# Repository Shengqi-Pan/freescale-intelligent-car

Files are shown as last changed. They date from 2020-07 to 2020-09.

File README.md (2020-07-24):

飞思卡尔全国大学生智能车竞赛 直立节能组

# 项目日志

## 6.24

1. 测定陀螺仪和加速度计bias和比例

2. 调通了卡尔曼滤波

3. 测定小车过轴线时的倾斜角，设定其为平衡角，23.8°

4. pd参数调节，最终角度确定为23.87°，角度环参数P=2000 D=50

## 6.25, 6.26

1. 调了下电磁，实现基础的转向

2. 控速有点迷，一直没找到bug，进展不大

## 6.27

1. 找到控速bug, 因为限幅使得控速的角度附加全部处于死区，调节不过来

其他可能导致bug的原因：

- P太大

- 角度梯度太小

- angle_bias太小

- 限幅值太小

- 设定速度太大

## 6.28

1. 找到了疯狂振动(拖拉机)的原因, 角度环的D太大, 从59改到13后没有问题

## 6.29

1. 调通了左圆环，步骤如下:

    - 判断是左圆环or右圆环

    - 判断前瞻到切点

    - 判断车轮到切点，并将控制权移交竖电感

    - 用陀螺仪判断转向转过90度，此时将控制权移交横电感

    - 自然出环，待添加出环时屏蔽圆环状态的代码

2. 右环电感归一系数待调

    - 可考虑加偏置而不是单纯归一化

    - 考虑将1中的第二第三两个判断条件直接去掉（或许加上这两个条件实际意义不大）

## 7.5

1. 完成了速度的部分提升

    - 重新分割转向pd，加大d的作用

    - 加入抱死安全措施

## 7.6

1. 在高速下进圆环初步实现，问题比较大

2. 控速换成了PI控速，控速较稳

3. 小弯转向飘逸待改进？

## 7.7

1. 初步实现圆环进入，具体方法为通过补偿在圆环切点电感值减小的特点，产生交汇移交控制权给竖电感完成进环

2. 加入出环屏蔽，但圆环出环形成循环，出环时漂移，需要解决

3. 圆环入环准确率还不高，考虑角度补偿

4. 通过减小圆环中的偏差值圆滑圆环的过弯，圆环中莫名其妙抱死？

5. 可调节的有判断圆环的条件，入环的延迟距离，竖电感的归一化值，竖电感转向的pd

## 7.8

1. 完成入环2.0版本，出环1.0版本

    - 入环通过差值先减小后增大的现象设定阈值，完成入环的判断。

    - 出环通过减小出环时的deviation，同时增大d以补偿减小的deviation。

## 7.9 

1. 中断时间从1.25ms改为1.5ms

## 7.10

1. 通过限制angle_bias完成了过坡

2. 判坡用了个临时条件，最终决定加中间电感

## 7.14

1. 加入加速度计限幅，上下坡明显改善，直立环很硬

## 7.15

1. 杆子降低，速度回归，重调了转向和直立环

2. 去掉了转向陀螺仪补偿，入弯减速去掉但会掉速

3. 需要解决转弯减速的问题

## 7.16-7.23

一直在调结构改板子

## 7.24

1. 换新的电机调了一套比较好的pd，有时候转弯完全眼瞎，待调

> 看一下目前的代码和以往代码的区别，可能还存在一些能提高车辆稳定性的异常处理思路:
17代码：
    1. 编码器的加速度对加速度计的修正
    2. 陀螺仪零飘测定，或许会有效果吧？不加问题也不大
    3. 入弯低头补偿掉速，出弯抬头减速
    4. 速度超出允许最大速度一定值（200，400等），强制抬头

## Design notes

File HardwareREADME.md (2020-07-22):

# **硬件设计与调试**

## PCB Version 3.0

电磁检测插在MCU母板上

不带5V和12V稳压的电机驱动

底盘换成PCB，把无线充电方案、5V、12V稳压和MCU母板放上去

-----------------------------;

无线充电方案

## **TODO LIST**

### **母板V2.0和电磁检测V2.0板子硬件调试**

- ~~更换左侧竖电感~~

- ~~调节四个电位器，使左右横竖电感的AD采样值对称~~

- ~~直立控制测试~~

- ~~无线串口接收测试~~

---------------------

**7.14~7.16：基本正常**

---------------------

**已更换新版，该版母板和电磁寿终正寝。**

### 车底盘，PCB上把5V、12V稳压、母板放在一起

- ~~5V和12V输出的单点接地 SGND、PGND~~

- ~~按键S2~S5、RST封装修改~~

- ~~供电开关按键修改，要能流通大电流~~

- ~~可能需要修改电机控制、编码器、陀螺仪、无线串口的接口位置~~

- ~~需要增大一些接口之间的间距，以避免排线插接冲突~~

- ~~TPS630701封装修改，便于焊接和虚焊检查~~

- ~~检查供电接入开关、母板5V开关、驱动板12V开关是否加进去了~~

- ~~TPS61088封装修改~~

- ~~PCB尺寸定义与检查~~

- ~~给ICM留出2.5*1.5的空间~~

-------------------------------;

**7.15：车底盘，母板v4.0已制板**

-------------------------------;

**7.19：TPS61088升压12V无输出，计划7.20重焊，再测试一下thermal pad焊盘和PGND的连通性**

- 理一下国赛电路合集里面的61088升压

- 修改大电流回路的一些器件封装，包括电感换成功率电感。

- 板子上加入日期

**7.19：烧了两块TPS61088（有一段时间能够正常输出过），目前还没有查出问题出在哪里，拿TPS630701的输出接了EN脚，又把630701烧了......**

-------------------------------;

**7.20：准备更换12V稳压芯片方案**

- 除复位键按钮，剩余按钮改为拨码开关

- 稳压的5v可以考虑直接供给单片机，尽量不出现一个端子接两线的情况

- 主板的电感为六路电感，主板ad读取接口可以加上P06, P12, P16，上面三个引脚没有其它用处的话作为六路电感多出的两个电感

- 若单片机需要控制充电，任意空闲的GPIO留出作为控制引脚

- 也可多留两个废物引脚当备胎

- 可以考虑加蜂鸣器，P37，参考逐飞

### 电磁检测PCB

- 多加一个OPA2350，增加一路电感AD采样用于判坡

- 在母板上留出的尺寸空间也要作修改

- ~~**！！！要修改滤波的方式，更改输出滤波电路，RC串联加稳压和反向限幅**~~

- ~~**直接修改OPA2350为OPA4377，增加一路电感，暂时空出一路**~~

- ~~**加一路OPA2350，仿照OPAMOD模块**~~

----------------------------;

**7.13：电磁检测v2.0已改完制板，贴片电阻改为0603封装，电容为C0805**

**7.17：焊完了电磁检测的板子，毛刺问题、电磁测量值的非线性问题。**

----------------------------;

### 电机驱动板

----------------------------;

**7.16：焊接和调试，发现一个小问题：由于自举电容的机制约束，HIP4082驱动全桥的上管在原理上应该不能到100%占空比，这一点需要在之后的软件里面测试和注意。**

**7.20：在考虑是否把电机和驱动分两块芯片供电，34063升压可能电流负载能力不足。**

### 无线充电方案

- 恒功率充电 or 简单的全桥整流？

---------------------------;

**7.17：目前的想法是，接收端640KHZ LC谐振，然后四个肖特基二极管全桥整流，再稳压到12V，再接入SuperCap组，在线路上做电压电流的采样，送入单片机做乘积得到实时功率，然后PID控制MOS通断（BUCK）来控制平均充电电流（或者电压），做到稳定充电功率的效果**

**References：**

> [飞思卡尔恒功率无线充电（上）](https://cloud.tencent.com/developer/article/1651860) \
> [飞思卡尔恒功率无线充电（中）](https://cloud.tencent.com/developer/article/1651861) \
> [飞思卡尔恒功率无线充电（下）](https://cloud.tencent.com/developer/article/1651862)

**7.19：芯片选型**

- 备选器件

  - 前期12V转5V稳压：TPS5410，REG104，TPS561201

  - 全波整流转12V：TPS54360（需要额外注意设定其开关频率）

  - 电容：NPO高频电容

  - 电感：功率电感

**7.20凌晨：电路原理图基本完成，下一步更新封装和画PCB**

### 元器件

- OPA2350

- 100K电位器

- 稳压管

- 47K电阻

- TPS630701

- 61088外围电路元件RLC

- 工字电感

--------------------------;

**7.16：买了新一批器件**

**7.19：准备更换外围无源元件选型**

- 贴片陶瓷电容

- NPO高频电容

- 闭环控制、电压检测、反馈回路的电阻均要换成高精度低温漂电阻

**7.20凌晨：准备买元件**

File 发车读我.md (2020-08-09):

# 拨码开关

|拨码作用|左侧|右侧|
|---|---|---|
|出库方向|向左出入库|向右出入库|
|速度1|正常速度|快速|
|速度2|慢速|最慢|
|圆环开关|开|关|
|充电电量|少|多|
|充电电量|开|关|

# 摄像头

屁股坐地上摄像头面向正前方，不直掰一掰

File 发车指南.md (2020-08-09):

# 裁判手册中的说明

比赛流程控制：

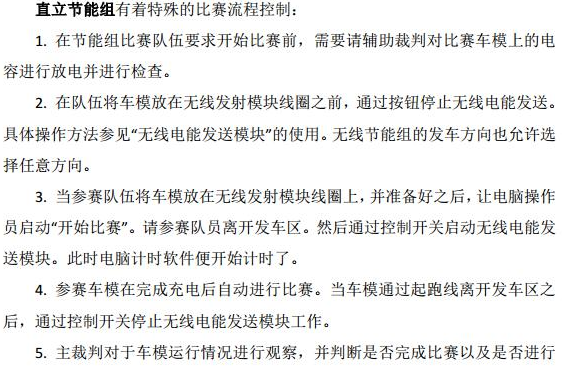
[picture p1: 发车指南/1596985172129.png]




充电线圈的标志可能如下，十字代表中心：

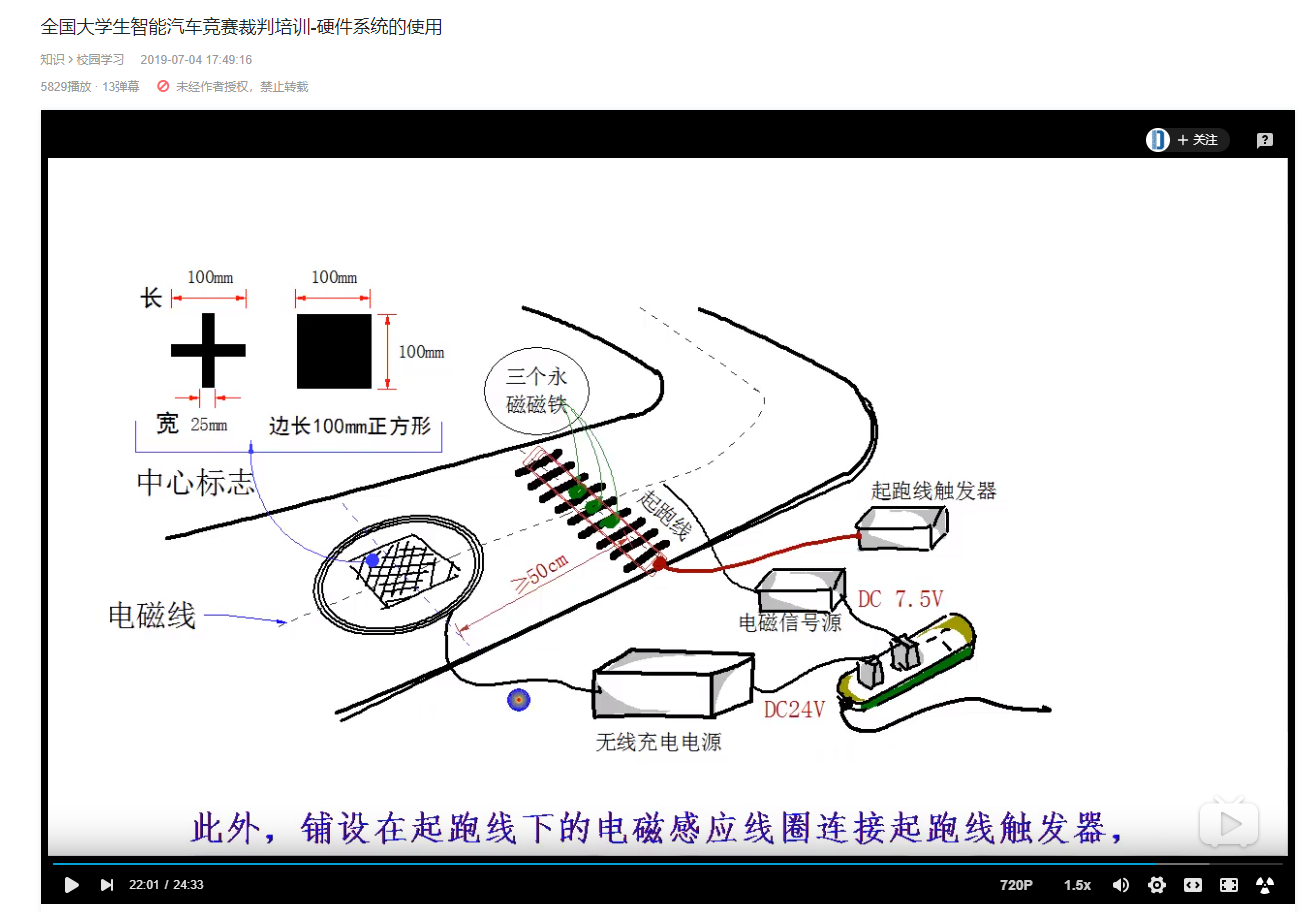
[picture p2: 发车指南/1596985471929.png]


# 试车阶段需要做的事情

1. 找一个好的出库方向试跑一圈

2. **接上无线串口并在电脑上打开示波器点击run和绿色的运行，打开isp烧录软件**
3. 大概1min时间摸一摸最优的充电位置，注意放电到0再充电
4. 目测圆环大小，烧录圆环测试代码并推行测试，

# 发车检查

**拔掉无线串口！！！！！！**

1. 擦轮并检查两轮轴固定，如下图：

   - 轮胎前后转动齿轮跟随良好
   - 轮胎左右位置固定，即轮胎不会往外拉出来

   

2. 检查摄像头

   - 是否打开，是否90度（如果当前角度入库过晚，考虑把固定的胶撕下来（不要脱落），ccd变为90度）

3. 检查电机驱动是否打开（摁下），电源总开关是否打开（向下），五伏开关是否打开（向右）

4. T头是否全部插紧

5. 外部飞出的导线是否会磨到齿轮

6. 拨码开关拨到适当的位置，第一圈跑应当除了第一个拨码开关控制左右出库（视情况而定）外，全部打向左侧

7. 检查其他接线是否牢固，此项基本问题不大，注意编码器即可

8. 将车辆摆放到正确的位置

# 应急处理

**若车辆冲出赛道，不计成绩的情况，立刻重新发车**

1. 第一圈跑完可能出现的情况及应对方式：

   - 出库偏晚或偏早

     换代码，视频沟通，直接**烧代码**即可

   - 进圆环跑飞，跑出赛道外

     立刻停车并**关闭圆环拨码**4，尝试完成比赛，与此同时btk根据现象修改圆环代码，烧录并发车

   - 入库偏早或偏晚

     偏早不太可能吧...

     偏晚的话调节摄像头到平行位置应该就可，如果上坡摄像头磕到改变角度可以考虑用螺丝刀和十字架**把摄像头上下旋转的控制螺丝螺母拧紧**

   - 电量不够跑完一圈赛道

     视距离终点的距离而定能量拨码 ：距离不远->6拨码向右打，距离较远->5,6全部向右打，实在不行则烧代码。

   - 顺利跑完，8说了，i了i了

     用万用表检查一下跑完时还剩多少电压

     - 如果还剩电压比较多，如4v，将能量拨码5向右打，冲一圈。
     - 如果剩余电量不是很多，提速，将速度拨码2向右打，冲一圈

2. 其他情况应急处理

   - 电磁杆撞断：尝试用黑胶布补上，实在不行就用旧杆
   - 竖电感撞掉：尝试用黑胶布补上，不行就缠在杆子上，关闭圆环
   - 无法判库：尝试用距离进库

# 约定

如果改动要烧的代码涉及到拨码档：

- 比如需要的速度比拨码的最高档还要高，则改动的代码直接提高最高档位速度
- 如需要的速度比拨码最低档还要低，则改动的代码直接降低最低档位速度

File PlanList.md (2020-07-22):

# **PLAN LIST**

## **7.21**

- 软件：新底盘调控速2000，直道、弯道、上下坡

- 硬件：改底盘

  - 电感改成功率电感封装

  - 630701外围电路换成63070，加两个电阻

  - 5V稳压加个防倒灌环节（参考别的技术报告）

  - 61088的GND、VIN、VOUT铺铜走线调整

  - 再留出两路AD给电流采样电阻的正负电压

- 硬件：买元器件

  - 功率电感1.5uH

  - TPS63070

  - TPS561201

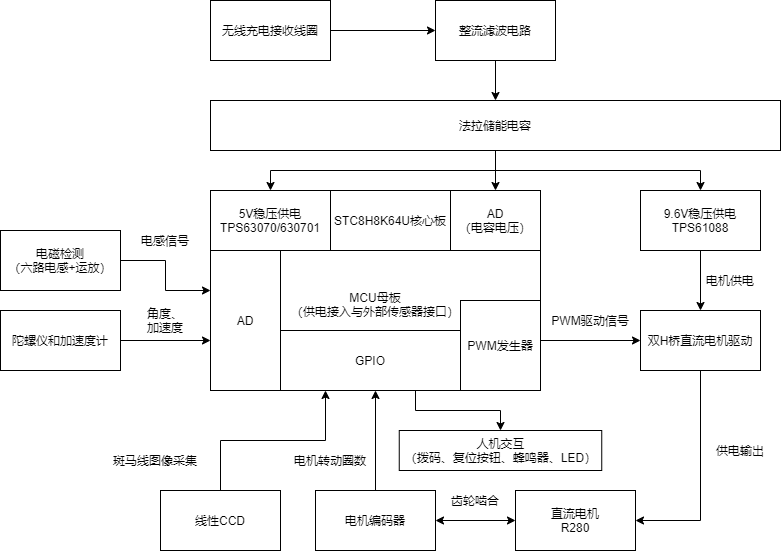
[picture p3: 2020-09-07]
硬件模块总览.png

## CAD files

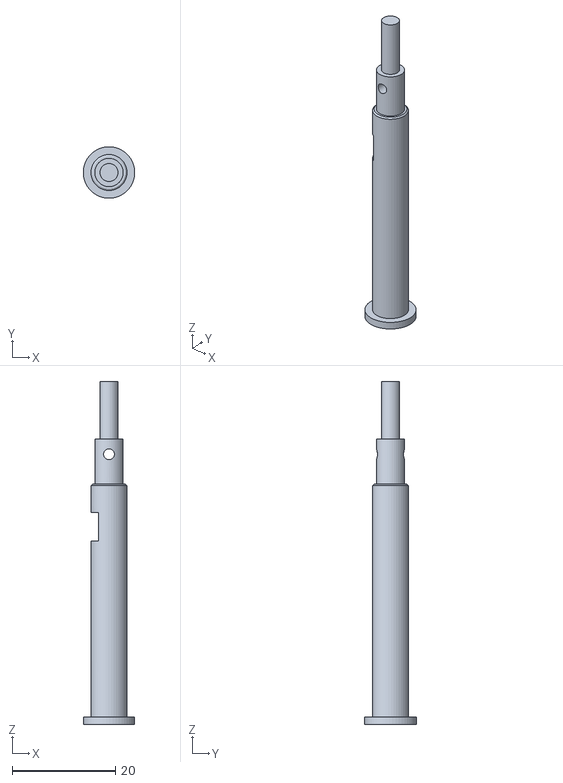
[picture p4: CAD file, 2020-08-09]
轮胎轴3D打印模型/3.stl
9.98 x 10.00 x 66.6

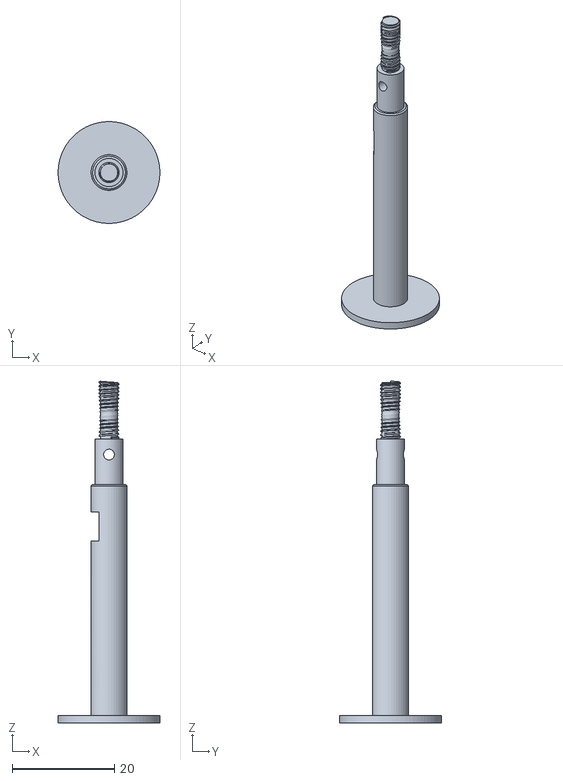
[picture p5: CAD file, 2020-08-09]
轮胎轴3D打印模型/2.stl
19.9 x 19.9 x 66.9

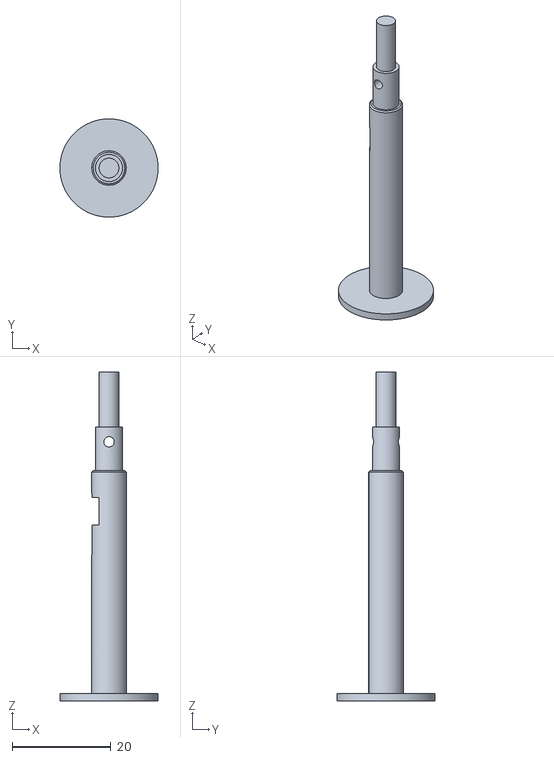
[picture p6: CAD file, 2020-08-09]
轮胎轴3D打印模型/1.stl
19.9 x 19.9 x 66.6

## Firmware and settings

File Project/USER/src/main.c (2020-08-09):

/*********************************************************************************************************************
 * COPYRIGHT NOTICE
 * Copyright (c) 2020,逐飞科技
 * All rights reserved.
 * 技术讨论QQ群：一群：179029047(已满)  二群：244861897(已满)  三群：824575535
 *
 * 以下所有内容版权均属逐飞科技所有，未经允许不得用于商业用途，
 * 欢迎各位使用并传播本程序，修改内容时必须保留逐飞科技的版权声明。
 *
 * @file            main
 * @company         成都逐飞科技有限公司
 * @author          逐飞科技(QQ790875685)
 * @version         查看doc内version文件 版本说明
 * @Software        MDK FOR C51 V9.60
 * @Target core     STC8H8K64S4
 * @Taobao          https://seekfree.taobao.com/
 * @date            2020-06-01
 ********************************************************************************************************************/

#include "headfile.h"
#include "icm20602.h"
#include "car_info.h"
#include "kalman.h"
#include "motor.h"
#include "encoder.h"
#include "control.h"
//board.h文件中FOSC的值设置为0,则程序自动识别系统频率

/*board.h文件中FOSC的值设置不为0，则系统频率为FOSC的值，
在使用stc-isp工具下载程序的时候需要将IRC频率设置为FOSC的值*/

/*在board_init中,已经将P54引脚设置为复位，
如果需要使用P54引脚,可以在board.c文件中的board_init()函数中删除SET_P54_RESRT即可*/
void main()
{
    DisableGlobalIRQ();  //  关闭总中断
    board_init();  // 初始化寄存器
    pit_timer_us(TIM_1, 1500);  // 使用TIMER作为周期中断，时间1.5ms一次
    icm20602_init_simspi();  // icm20602初始化, 引脚查看宏定义
    seekfree_wireless_init();  // 无线串口初始化
    motor_init();  // 电机初始化
    l_init();  // ad初始化
    // adc_init(ADC_P15, ADC_SYSclk_DIV_2);
    encoder_init();  // 编码器初始化
    ccd_init();  // 线性ccd初始化
    delay_ms(10);
    EnableGlobalIRQ(); //  开启总中断
    while(1)
    {
        // 上位机示波器查看
        // data_conversion(ad[0], car_info.speed.left, car_info.speed.right, car_info.speed.average, virtual_scope_data);
        // uart_putbuff(WIRELESS_UART, virtual_scope_data, sizeof(virtual_scope_data));
        // seekfree_wireless_send_buff(virtual_scope_data, sizeof(virtual_scope_data));
        // ccd_send_data(WIRELESS_UART, ccd_data);
    }
}

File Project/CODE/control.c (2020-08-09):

/*******************************************
 * @file            control
 * @note            控制相关的函数，包括直立，速度，转向
 * @author          psq&btk
 * @software        MDK
 * @target core     STC8H8K64S4
 *******************************************/

#include "control.h"
int16 ad_test[4] = {0, 0, 0, 0};

/***************************
 * @breif   角度控制函数
 * @param   car_angle, car_w      卡尔曼滤波得到的角度和角速度
 * @param   angle_set             给角度
 * @return  控直立的电机占空比
 * @note    
 * @author  btk
 ***************************/
float angle_control(float car_angle, float car_w, float angle_set)   //控直立
{
    static float motor_angle_control, angle_control;
    angle_control = car_angle - angle_set;
    if(car_info.state == TAKE_OFF)         //起步时p，d应用独立参数
        motor_angle_control = angle_control * ANGLE_CONTROL_P_BEGIN + car_w * ANGLE_CONTROL_D_BEGIN + 2000;
    else if(car_info.state == STOP)
        motor_angle_control = 100;
    if(car_info.state == RAMP_UP || car_info.state == RAMP_DOWN)       //过坡时减p加d
        motor_angle_control = angle_control * ANGLE_CONTROL_P + car_w * ANGLE_CONTROL_D + 5000;
    else
        motor_angle_control = angle_control * ANGLE_CONTROL_P + car_w * ANGLE_CONTROL_D;
    return motor_angle_control;
}

/***************************
 * @breif   速度控制函数
 * @param   speed_real      左右轮转速真实值取平均
 * @param   speed_set       给定速度
 * @return  控速附加角
 * @note    
 * @author  psq
 ***************************/
float speed_control(int16 speed_real, int16 speed_set)
{
    static float angle_bias = 0, angle_bias_last = 0;
    static int16 speed_deviation, speed_deviation_integrate;
    static int8 integrate_discard_cnt;          //积分项定时清0
    speed_deviation = speed_real - speed_set;  // 实际速度和设定速度差值
    if(++integrate_discard_cnt == 20)           //30ms清一次0
    {
        integrate_discard_cnt = 0;
        speed_deviation_integrate = 0;
    }
    speed_deviation_integrate += speed_deviation;   //积分项累加
    switch (car_info.state)
    {
        case TAKE_OFF: case STRAIGHT_AHEAD: 
        /************直道控速************/
            if(speed_real < 1200)
            {
                angle_bias = -speed_deviation * SPEED_CONTROL_P;
            }
            else
            {
                angle_bias = -(speed_deviation * SPEED_CONTROL_P + speed_deviation_integrate * SPEED_CONTROL_I);
            }
            break;
        case INTO_TURN: case RING:
        /************出/入弯控速************/
            // TODO:参数待调
            angle_bias = -(speed_deviation * SPEED_CONTROL_P + speed_deviation_integrate * SPEED_CONTROL_I);
            angle_bias -= 4;
            break;
        case IN_TURN: 
        /************弯中控速************/
            // TODO:参数待调
            angle_bias = -(speed_deviation * SPEED_CONTROL_P + speed_deviation_integrate * SPEED_CONTROL_I);
            angle_bias -= 7;
            break;
        case RAMP_UP:
        /************上坡************/
            if(speed_real < 1200)
            {
                angle_bias = -speed_deviation * SPEED_CONTROL_P;
            }
            else
            {
                angle_bias = -(speed_deviation * SPEED_CONTROL_P + speed_deviation_integrate * SPEED_CONTROL_I);
            }
            break;
        case RAMP_DOWN:
        /************下坡************/
            // if(speed_real < 1200)
            // {
            //     angle_bias = -speed_deviation * SPEED_CONTROL_P;
            // }
            // else
            // {
            //     angle_bias = -(speed_deviation * SPEED_CONTROL_P + speed_deviation_integrate * SPEED_CONTROL_I);
            // }
            return -20;
            break;
        case STOP:
            angle_bias = -(speed_deviation * SPEED_CONTROL_P + speed_deviation_integrate * SPEED_CONTROL_I);
        default:
            return 0;
            break;
    }

    /************限制bias变化防止突变************/
    if (angle_bias - angle_bias_last > 0.1)
        angle_bias = angle_bias_last + 0.1;
    else if (angle_bias - angle_bias_last < -0.1)
        angle_bias = angle_bias_last - 0.1;
    /*if(car_info.state == TAKE_OFF)              //起步限制偏差角，防止起步过猛
    {
        angle_bias = angle_bias>12 ? 12 : angle_bias;
        angle_bias = angle_bias<-12 ? -12 : angle_bias;
    }*/
    if(angle_bias > 7 && speed_real < 1600)
       angle_bias = 7;
    angle_bias_last = angle_bias;
    return angle_bias;
}

/*
观察电磁读取的ad值，便于后面处理，不出现在主函数中
*/
void induc_test(void)
{ 
    getl_once();
    ad_test[0] = (4*ad_test[0] + l_h_1)/5;
    ad_test[1] = (4*ad_test[1] + l_h_2)/5;
    ad_test[2] = (4*ad_test[2] + l_s_1)/5;
    ad_test[3] = (4*ad_test[3] + l_s_2)/5;
}
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

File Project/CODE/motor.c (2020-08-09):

/*******************************************
 * @file            motor
 * @note            基于逐飞pwm的电机底层驱动
 * @author          btk
 * @software        MDK
 * @target core     STC8H8K64S4
 *******************************************/
#include "motor.h"

void motor_init(void)
{
    pwm_init(PWM5_P00,  17000, 0); //初始化PWM0  使用P00引脚  初始化频率为17Khz
	pwm_init(PWM6_P01,  17000, 0); //初始化PWM0  使用P01引脚  初始化频率为17Khz
	pwm_init(PWM2P_P22, 17000, 0); //初始化PWM2  使用P22引脚  初始化频率为17Khz
	pwm_init(PWM4P_P26, 17000, 0); //初始化PWM2  使用P26引脚  初始化频率为17Khz
}

void motor_output(float motor_angle_control, int16 motor_turn_control)
{
    float motor_left, motor_right;
    static float motor_left_old = 0, motor_right_old = 0;
    motor_left = motor_angle_control - motor_turn_control;
    motor_right = motor_angle_control + motor_turn_control;  
    motor_left = motor_left>0 ? motor_left + 70 : motor_left - 70; //电机转差补偿，补偿1.5%
    motor_right = motor_right>0 ? motor_right - 70 : motor_right + 70;
    /*if(motor_left - motor_left_old >= 1000)
        motor_left = motor_left_old + 1000;
    else if(motor_left - motor_left_old <= -1000)
        motor_left = motor_left_old - 1000;
    if(motor_right - motor_right_old >= 1000)
        motor_right = motor_right_old + 1000;
    else if(motor_right - motor_right_old <= -1000)
        motor_right = motor_right_old - 1000;*/
    motor_left_old = motor_left;
    motor_right_old = motor_right;
    if(motor_left > AMPLITUDE_LIMIT)
        motor_left = AMPLITUDE_LIMIT;
    else if(motor_left < -AMPLITUDE_LIMIT)
        motor_left = -AMPLITUDE_LIMIT;
    if(motor_right > AMPLITUDE_LIMIT)
        motor_right = AMPLITUDE_LIMIT;
    else if(motor_right < -AMPLITUDE_LIMIT)
        motor_right = -AMPLITUDE_LIMIT;
    if(motor_left > 0)
    {
        motor_left += DEAD_TIME;
    }
    else if(motor_left < 0)
    {
        motor_left -= DEAD_TIME;
    }
    if(motor_right > 0)
    {
        motor_right += DEAD_TIME;
    }
    else if(motor_right < 0)
    {
        motor_right -= DEAD_TIME;
    }
    if(motor_left >= 0)
    {
        pwm_duty(PWM5_P00, (int)motor_left + 1000); //右电机弱，补强2%的占空比
        pwm_duty(PWM6_P01, 1000);	
    }
    else
    {
        pwm_duty(PWM5_P00, 1000);
        pwm_duty(PWM6_P01, (int)(-motor_left) + 1000);	
    }
    if(motor_right >= 0)
    {
        pwm_duty(PWM2P_P22, (int)motor_right + 1000);
        pwm_duty(PWM4P_P26, 1000);	
    }
    else
    {
        pwm_duty(PWM2P_P22, 1000);
        pwm_duty(PWM4P_P26, (int)(-motor_right) + 1000);	
    }
    /*if(motor_left >= 0)
    {
        pwm_duty(PWM5_P00, (uint16)(10000 - motor_left));
        pwm_duty(PWM6_P01,  0);
    }
    else
    {
        pwm_duty(PWM5_P00, (uint16)(10000 + motor_left));
        pwm_duty(PWM6_P01,  10000);
    }
    if(motor_right >= 0)
    {
        pwm_duty(PWM2P_P22, (uint16)(10000 - motor_right));
        pwm_duty(PWM4P_P26,  10000);
    }
    else
    {
        pwm_duty(PWM2P_P22, (uint16)(10000 + motor_right));
        pwm_duty(PWM4P_P26,  0);
    }*/
}

void motor_stop()
{
    /*pwm_duty(PWM5_P00,  1000); //初始化PWM0  使用P00引脚  初始化频率为17Khz
    pwm_duty(PWM6_P01,  2500); //初始化PWM0  使用P01引脚  初始化频率为17Khz
    pwm_duty(PWM2P_P22, 1000); //初始化PWM2  使用P22引脚  初始化频率为17Khz
    pwm_duty(PWM4P_P26, 2500); //初始化PWM2  使用P26引脚  初始化频率为17Khz
    delay_ms(800);*/
    while (1)
    {
        pwm_duty(PWM5_P00,  1000); //初始化PWM0  使用P00引脚  初始化频率为17Khz
        pwm_duty(PWM6_P01,  1000); //初始化PWM0  使用P01引脚  初始化频率为17Khz
        pwm_duty(PWM2P_P22, 1000); //初始化PWM2  使用P22引脚  初始化频率为17Khz
        pwm_duty(PWM4P_P26, 1000); //初始化PWM2  使用P26引脚  初始化频率为17Khz
    }
}

/***************************
 * @breif   闭环停车
 * @param   void
 * @return  void
 * @note    入库后闭环刹车
 * @author  psq
 ***************************/
void motor_stop_plus()
{
    int16 motor_left, motor_right;  
    int16 forward_cnt = 0;
    int16 forward_flag = 1;
    while (1)
    {
        if(forward_flag == 1 && ++forward_cnt == 200)
        {
            forward_flag = 0;
            pwm_duty(PWM5_P00,  4000); //初始化PWM0  使用P00引脚  初始化频率为17Khz
            pwm_duty(PWM6_P01,  1000); //初始化PWM0  使用P01引脚  初始化频率为17Khz
            pwm_duty(PWM2P_P22, 4000); //初始化PWM2  使用P22引脚  初始化频率为17Khz
            pwm_duty(PWM4P_P26, 1000); //初始化PWM2  使用P26引脚  初始化频率为17Khz
            delay_ms(300);
        }
        car_info.speed = get_speed(5);
        motor_left = -MOTOR_STOP_P * car_info.speed.left;
        motor_right = -MOTOR_STOP_P * car_info.speed.right;
        if(car_info.speed.left < 50 && car_info.speed.left > -50)
            motor_left = 0;
        if(car_info.speed.right < 50 && car_info.speed.right > -50)
            motor_right = 0;
       
        if(motor_left > AMPLITUDE_LIMIT)
            motor_left = AMPLITUDE_LIMIT;
        else if(motor_left < -AMPLITUDE_LIMIT)
            motor_left = -AMPLITUDE_LIMIT;
        if(motor_right > AMPLITUDE_LIMIT)
            motor_right = AMPLITUDE_LIMIT;
        else if(motor_right < -AMPLITUDE_LIMIT)
            motor_right = -AMPLITUDE_LIMIT;
        if(motor_left >= 0)
        {
            pwm_duty(PWM5_P00, (int)motor_left + 1000); //右电机弱，补强2%的占空比
            pwm_duty(PWM6_P01, 1000);	
        }
        else
        {
            pwm_duty(PWM5_P00, 1000);
            pwm_duty(PWM6_P01, (int)(-motor_left) + 1000);	
        }
        if(motor_right >= 0)
        {
            pwm_duty(PWM2P_P22, (int)motor_right + 1000);
            pwm_duty(PWM4P_P26, 1000);	
        }
        else
        {
            pwm_duty(PWM2P_P22, 1000);
            pwm_duty(PWM4P_P26, (int)(-motor_right) + 1000);	
        }
        delay_ms(5);
    }
    else
    {
        pwm_duty(PWM5_P00, 1000);
        pwm_duty(PWM6_P01, (int)(-motor_left) + 1000);	
    }
    if(motor_right >= 0)
    {
        pwm_duty(PWM2P_P22, (int)motor_right + 1000);
        pwm_duty(PWM4P_P26, 1000);	
    }
    else
    {
        pwm_duty(PWM2P_P22, 1000);
        pwm_duty(PWM4P_P26, (int)(-motor_right) + 1000);	
    }
    delay_ms(5);
}

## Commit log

2020-06-18 stage works
    [SEEKFREE_18TFT.obj, SEEKFREE_ABSOLUTE_ENCODER.obj, SEEKFREE_FONT.obj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]
2020-06-19 add acc sensor
    [SEEKFREE_18TFT.obj, SEEKFREE_ABSOLUTE_ENCODER.obj, SEEKFREE_FONT.obj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]
2020-06-19 add gyro
    [icm20602.obj, main.obj]
2020-06-21 add .gitignore and car info
    [SEEKFREE_18TFT.obj, SEEKFREE_ABSOLUTE_ENCODER.obj, SEEKFREE_FONT.obj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]
2020-06-22 加入motor.c motor.h
2020-06-22 加点注释
2020-06-22 增加了电磁读取用的函数
2020-06-22 修正了加速度计的角度值
2020-06-22 tab 改空格
2020-06-22 修改下ad文件
2020-06-22 删除了临时文件，修改了gitignore规则
2020-06-24 定时时间最少3ms，再少就出不了中断
2020-06-24 修改变量名
2020-06-24 陀螺仪和加速度计校准
2020-06-24 平衡角测定
2020-06-24 进一步PD调节，小车基本稳定，抗干扰有待加强
2020-06-24 没写完的半成品
2020-06-25 修改细节
2020-06-25 优化文件结构，修改细节
2020-06-25 中转半成品
2020-06-25 调试电磁，将代码导过去
2020-06-25 增加控速的接口
2020-06-25 调下电磁 暂时存放
2020-06-25 转弯有时会错乱，具体原因需要进一步排查
2020-06-25 增加了编码器的驱动以及控速，但有bug待修复
2020-06-26 现在用于检测电感 并检查版本
2020-06-26 完成初步控直立
2020-06-26 将电磁转向加入，参数等待进一步调节
2020-06-27 改变了限幅值和角度环P
2020-06-27 直立不对 pull解决一下
2020-06-27 完成控速，之前失败原因为限幅太小，P太大导致控速大部分都在死区
2020-06-27 添加项目日志
2020-06-27 加入了弯道和上下坡控速，尚未测试
2020-06-27 加入了模糊pd，但未调试
2020-06-27 实现控直立 100~2000m/s经测试都ok，但还是偶尔会失控，未能超出此bug
2020-06-28 实现了简单的控速+转向控制
2020-06-28 写好模糊pd 准备融合成为婴儿车
2020-06-28 减小角度环P, 修复振动bug, 窜到需要解决
2020-06-28 减小角度环D, 修复振动bug, 窜道需要解决
2020-06-28 试一下圆环第一步
2020-06-28 进行到判断圆环切点
2020-06-29 加入圆环，右圆环有待商榷
2020-07-02 准备简化程序，暂时存档
2020-07-04 正在进行转向pd调参
2020-07-04 在1.7m到1.8m的情况连续过弯不行，其余情况还可以
2020-07-04 增加陀螺仪补偿抑制转弯加速
2020-07-04 一套较好的参数
2020-07-04 上坡之前表现较好，在下坡之后连续弯会跑出赛道
2020-07-05 能减速的控速参数
2020-07-05 加入转弯减速（直道1.8转弯1.）
2020-07-06 加入pi调速，速度控制情况有所改善，但存在颠簸之后起飞的现象
2020-07-06 十分初步的圆环
2020-07-06 除了圆环都还可以
2020-07-07 能够判别出圆环，但会反复进入环中
2020-07-07 加入出环岛屏蔽再次判环岛
2020-07-07 初级圆环
2020-07-08 圆环入环效果已经较好，能够定出角度，等待进一步处理
2020-07-08 可以单向出环，另一个方向待调，需要进一步观察电感值
2020-07-08 圆环基本over，需要进一步完善入环条件
2020-07-09 中断时间改为1.5ms
2020-07-10 初步过坡，很容易误判，平时跑记得注释掉
2020-07-11 准备去除冗余代码
2020-07-11 加一些注释
2020-07-11 改了距离，转向角积分的接口，删去冗余代码
2020-07-11 增加硬件设计与调试日志
2020-07-12 修改硬件调试日志，增加TODO LIST
2020-07-12 出库初步，电磁阴间，待调，准备入库
2020-07-12 更改电磁检测板
2020-07-13 更新硬件设计进度
2020-07-14 加速度计变化率限幅，带突破
2020-07-14 准备对电感进行角度耦合
2020-07-14 更新硬件调试日志
2020-07-16 换板子之后重调了参数
2020-07-16 修正了圆环，准备提速
2020-07-16 更换新的电磁后调好的转向参数
2020-07-16 更新无线充电部分
2020-07-17 加入圆环
2020-07-18 更新了底盘的一些问题
2020-07-19 加入中间横电感
2020-07-19 准备大型更换结构，并更换电机，存留代码备用
2020-07-19 更新硬件调试信息，增加无线充电待定和母板改动方案
2020-07-20 加入甲方要求
2020-07-20 更新硬件调试进度，加入母板V5.0方案
2020-07-20 新增计划表
2020-07-22 终点判断代码
2020-07-22 准备拉下ccd
2020-07-23 准备调小电机，用的逐飞驱动板
2020-07-24 添加17年代码可借鉴的异常处理
2020-07-24 初步调节了新的电机，并且写了充电的雏形
2020-07-26 终点判断条件确定，准备入库
2020-07-29 写好新的电机输出，并改变了抱死
2020-07-29 注释掉准备直立，改编码器
2020-07-30 修改编码器代码,用r2430自带编码器获取速度
2020-07-31 新电机一套勉强用的参数
2020-08-01 轮子脏能跑
2020-08-03 加入了入库
2020-08-03 此版本没问题，但控速p改为0.04，电机限幅增加到98，出现问题
2020-08-06 r2430的使命终止于此，r280归位
2020-08-07 280小试牛刀
2020-08-07 初步入库以及圆环判别条件 280电机速度稳定
2020-08-07 增加闭环刹车抱死
2020-08-08 圆环基本调好，入库下坡不行
2020-08-08 下坡趴死入库
2020-08-08 出库可以上坡
2020-08-08 微调了机械结构
2020-08-08 完全体1.0
2020-08-09 基本上是比赛代码1.0
2020-08-09 比赛代码1.1修改了出库
2020-08-09 更新发车指南
    [1.stl, 2.stl, 3.stl]
2020-08-09 目前赛前烧录的代码

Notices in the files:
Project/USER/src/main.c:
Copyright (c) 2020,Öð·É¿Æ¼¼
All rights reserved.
